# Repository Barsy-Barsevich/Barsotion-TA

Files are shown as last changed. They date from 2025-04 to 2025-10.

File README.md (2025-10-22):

# Barsotion-TA
Board computer for model rockets, the 11th board after Berkut

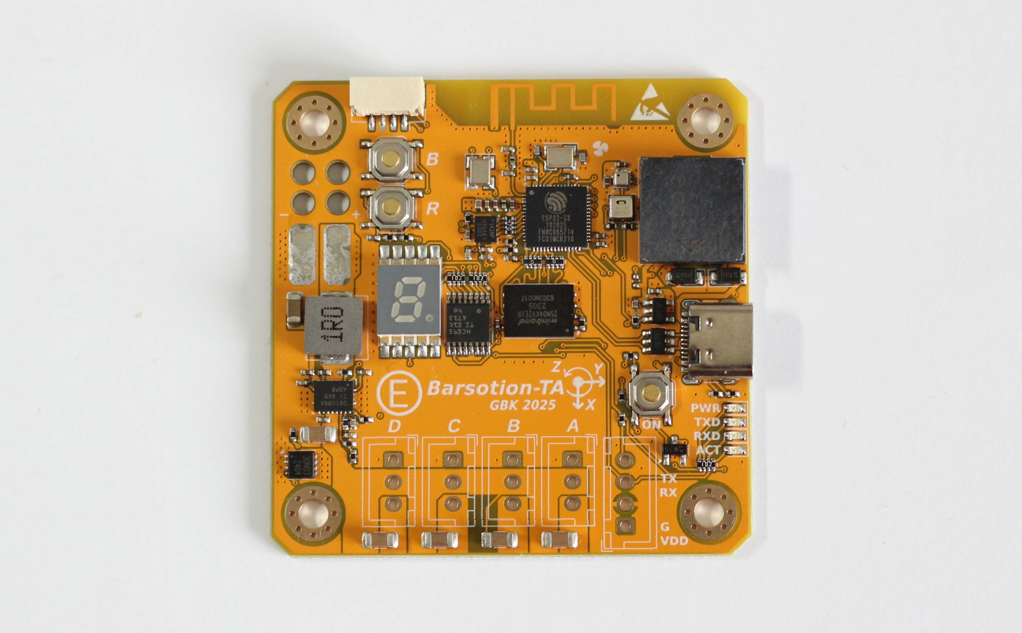
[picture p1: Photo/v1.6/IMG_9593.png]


## ⚡️Features
- Dual-core 240MHz Xtensa processor (in ESP32-S3)
- 512 MB log flash
- Up to 8kHz IMU cycle frequency
- Barometer, thermometer, hygrometer
- Onboard DC-DC pull-up converter for servos
- 2.4GHz Wi-Fi / Bluetooth / BLE antenna

## ⚡️Manual
- [EA&TA_user_manual_revD.pdf (newest revision)](./Manual/EA&TA_user_manual_revD.pdf)
- [EA&TA_user_manual_revC.pdf](./Manual/EA&TA_user_manual_revC.pdf)
- [EA&TA_user_manual_preliminary_edition_revB.pdf](./Manual/EA&TA_user_manual_preliminary_edition_revB.pdf)
- [EA&TA_user_manual_preliminary_edition_revA.pdf](./Manual/EA&TA_user_manual_preliminary_edition_revA.pdf)

## ⚡️Software
- [EA & TA software packet](https://github.com/Barsy-Barsevich/Barsotion-xA-software)

## ⚡️Continious progress
- [Previous board: Barsotion-EA](https://github.com/Barsy-Barsevich/Barsotion-EA)
- [Previous board: Barsotion-AH4](https://github.com/Barsy-Barsevich/Barsotion-AH4)

## ⚡️Schematic
[Full electrical schematic in .pdf](./Schematic/Barsotion-TA_Schematic_v1.6.pdf)
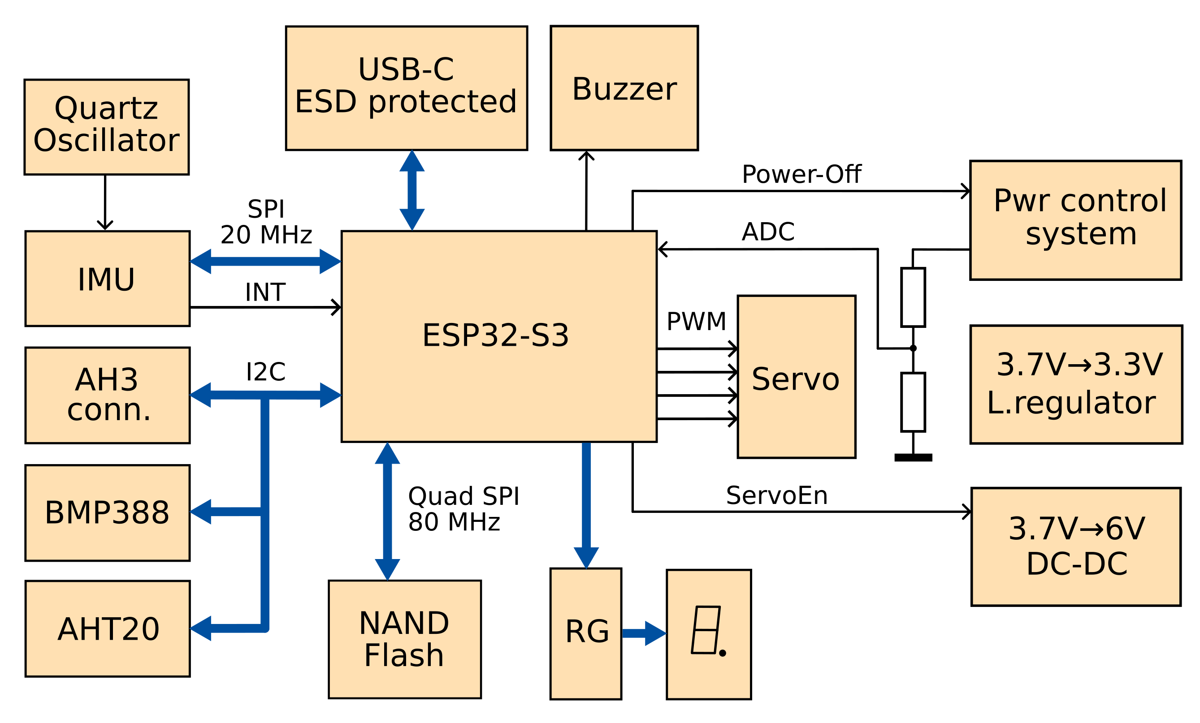
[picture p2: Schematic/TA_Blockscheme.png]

## ⚡️Parameters
- Microcontroller: ESP32-S3FN8 (2x Xtensa LX7 core)
- Clock frequency: 240MHz
- Gyroscope: on-board ICM-42688-P (SPI, interrupt channel)
- Barometer: on-board, BMP388 (I2C)
- Hygrometer: on-board, AHT20 (I2C)
- Memory: 4Gbit SPI NAND Flash W25N04KVZEIG (Quad SPI)
- Quartz Gyroscope's ODR frequency stabilization
- 2.4GHz Wi-Fi / Bluetooth / BLE antenna

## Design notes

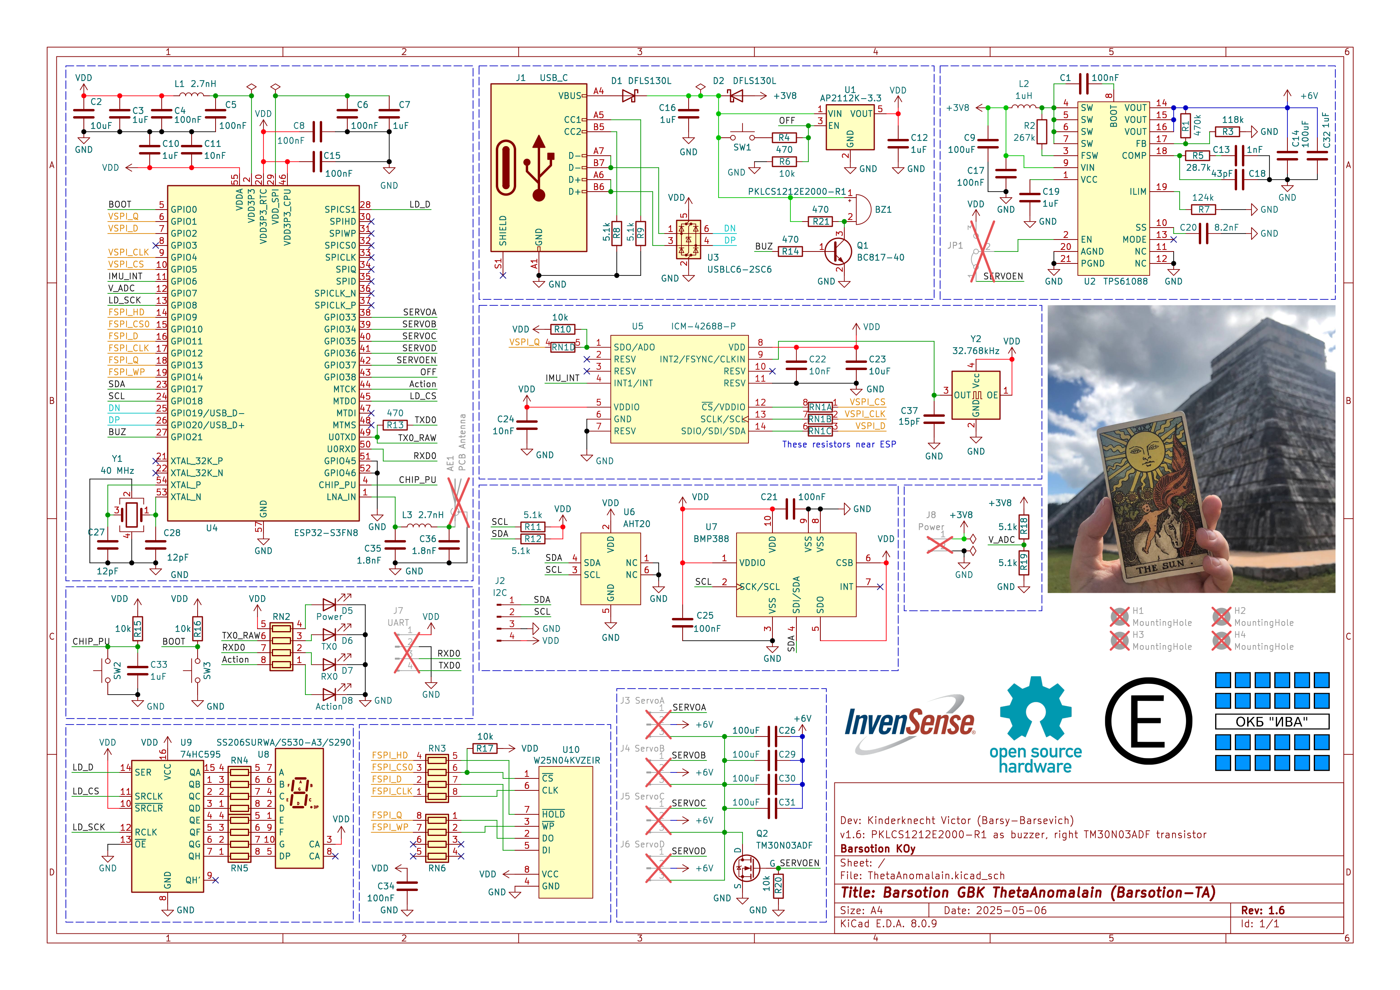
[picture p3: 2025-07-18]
Schematic/Barsotion-TA_Schematic_v1.6.png

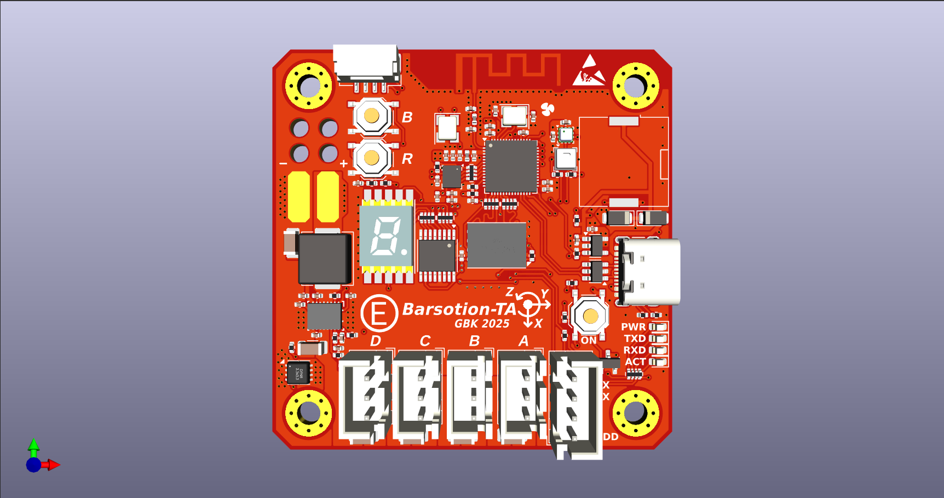
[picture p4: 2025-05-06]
Photo/v1.6/Screenshot at 2025-05-06 14-15-10.png

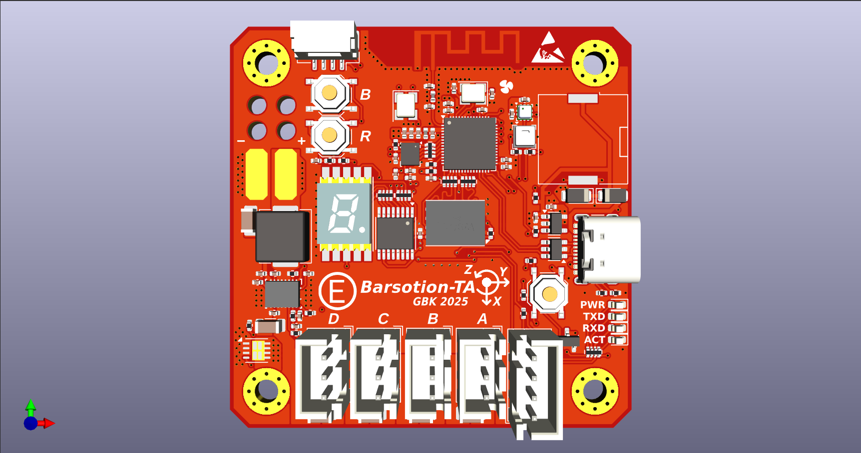
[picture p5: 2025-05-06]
Photo/v1.6/Screenshot at 2025-05-06 03-56-42.png

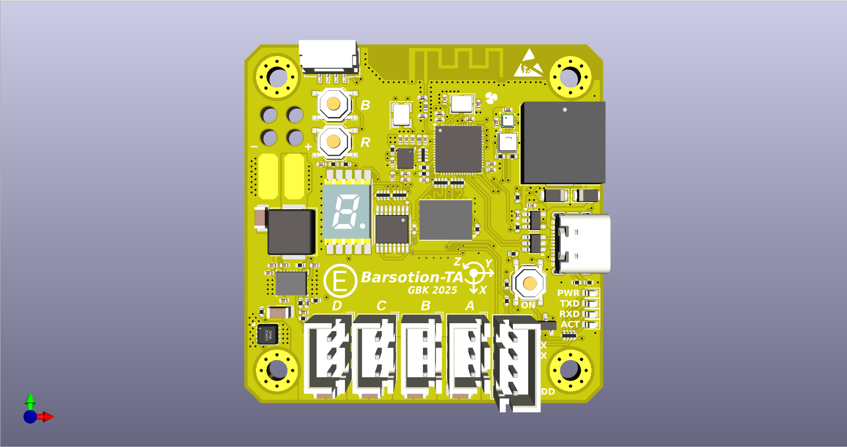
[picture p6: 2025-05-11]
Photo/v1.6/Screenshot at 2025-05-09 21-59-08.png

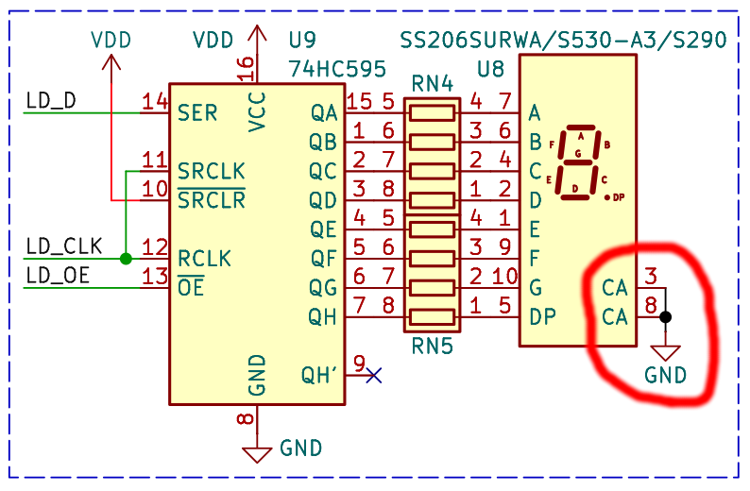
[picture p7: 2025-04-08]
Errors_EA/Screenshot at 2025-04-03 12-46-04.png

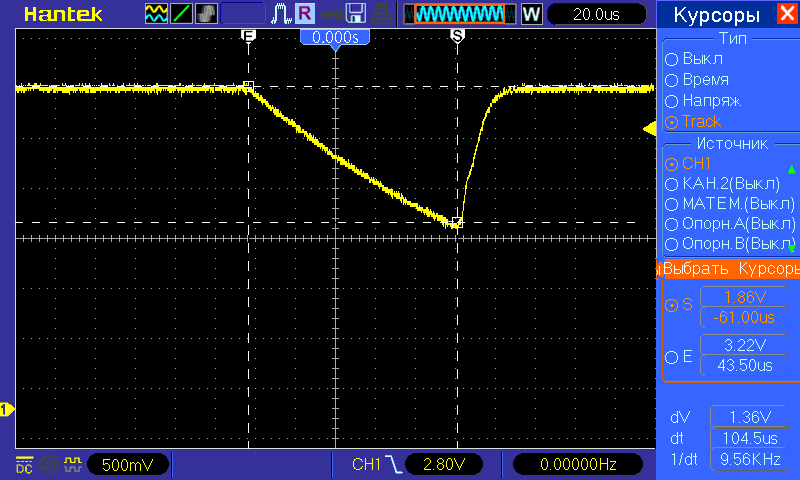
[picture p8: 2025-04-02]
Errors_EA/EA_Err1_Poweroff/VDD_line_when_POWER-OFF_command.bmp

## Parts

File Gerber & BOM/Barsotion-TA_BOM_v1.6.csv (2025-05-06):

Reference | Value | Datasheet | Footprint | Qty | Описание | Mfr.Part
BZ1 | PKLCS1212E2000-R1 | https://www.lcsc.com/datasheet/lcsc_datasheet_2410010302_Murata-Electronics-PKLCS1212E2000-R1_C184513.pdf | Buzzer_Beeper:Buzzer_Murata_PKLCS1212E | 1 | Buzzer | PKLCS1212E2000-R1
C1,C4,C5,C6,C8,C15,C17,C21,C25,C34 | 100nF | ~ | Capacitor_SMD:C_0402_1005Metric | 10 | Unpolarized capacitor
C2,C23 | 10uF | ~ | Capacitor_SMD:C_0402_1005Metric | 2 | Unpolarized capacitor
C3,C7,C10,C12,C16,C19,C32,C33 | 1uF | ~ | Capacitor_SMD:C_0402_1005Metric | 8 | Unpolarized capacitor
C9,C14,C26,C29,C30,C31 | 100uF | ~ | Capacitor_SMD:C_1206_3216Metric | 6 | Unpolarized capacitor
C11,C22,C24 | 10nF | ~ | Capacitor_SMD:C_0402_1005Metric | 3 | Unpolarized capacitor
C13 | 1nF | ~ | Capacitor_SMD:C_0402_1005Metric | 1 | Unpolarized capacitor
C18 | 43pF | ~ | Capacitor_SMD:C_0402_1005Metric | 1 | Unpolarized capacitor
C20 | 8.2nF | ~ | Capacitor_SMD:C_0402_1005Metric | 1 | Unpolarized capacitor
C27,C28 | 12pF | ~ | Capacitor_SMD:C_0402_1005Metric | 2 | Unpolarized capacitor
C35,C36 | 1.8nF | ~ | Capacitor_SMD:C_0402_1005Metric | 2 | Unpolarized capacitor
C37 | 15pF | ~ | Capacitor_SMD:C_0402_1005Metric | 1 | Unpolarized capacitor
D1,D2 | DFLS130L | ~ | Diode_SMD:D_PowerDI-123 | 2 | Schottky diode
D5 | Power | ~ | LED_SMD:LED_0603_1608Metric | 1 | Yellow Light emitting diode | TJ-S1608CY6T5ALC9Y-A5
D6 | TX0 | ~ | LED_SMD:LED_0603_1608Metric | 1 | Yellow Light emitting diode | TJ-S1608CY6T5ALC9Y-A5
D7 | RX0 | ~ | LED_SMD:LED_0603_1608Metric | 1 | Yellow Light emitting diode | TJ-S1608CY6T5ALC9Y-A5
D8 | Action | ~ | LED_SMD:LED_0603_1608Metric | 1 | Yellow Light emitting diode | TJ-S1608CY6T5ALC9Y-A5
J1 | USB_C | https://www.usb.org/sites/default/files/documents/usb_type-c.zip | Connector_USB:USB_C_Receptacle_GCT_USB4105-xx-A_16P_TopMnt_Horizontal | 1 | USB 2.0-only 16P Type-C Receptacle connector, mfr part TYPE C-DB-116PWB | TYPE C-DB-116PWB
J2 | I2C | ~ | Connector_JST:JST_GH_SM04B-GHS-TB_1x04-1MP_P1.25mm_Horizontal | 1 | Generic connector, single row, 01x04, script generated | A1257WR-S-4P
L1,L3 | 2.7nH | https://www.lcsc.com/datasheet/lcsc_datasheet_2409302232_APV-APH0630T1R0M_C5349700.pdf | Inductor_SMD:L_0402_1005Metric | 2 | Inductor
L2 | 1uH | https://www.lcsc.com/datasheet/lcsc_datasheet_2409302232_APV-APH0630T1R0M_C5349700.pdf | Inductor_SMD:L_APV_APH0630 | 1 | Power inductor | APH0630T1R0M
Q1 | BC817-40 | https://www.onsemi.com/pub/Collateral/BC818-D.pdf | Package_TO_SOT_SMD:SOT-23 | 1 | 0.8A Ic, 45V Vce, NPN Transistor, SOT-23
Q2 | TM30N03ADF | https://www.lcsc.com/datasheet/lcsc_datasheet_2411121142_Tritech-MOS-TM30N03ADF_C7422839.pdf | CustomPackage:PDFN3x3-8L | 1 | N-MOSFET transistor, TM30N03ADF | TM30N03ADF
R1 | 470k | ~ | Resistor_SMD:R_0402_1005Metric | 1 | Resistor
R2 | 267k | ~ | Resistor_SMD:R_0402_1005Metric | 1 | Resistor
R3 | 118k | ~ | Resistor_SMD:R_0402_1005Metric | 1 | Resistor
R4,R13,R14,R21 | 470 | ~ | Resistor_SMD:R_0402_1005Metric | 4 | Resistor
R5 | 28.7k | ~ | Resistor_SMD:R_0402_1005Metric | 1 | Resistor
R6,R10,R15,R16,R17,R20 | 10k | ~ | Resistor_SMD:R_0402_1005Metric | 6 | Resistor
R7 | 124k | ~ | Resistor_SMD:R_0402_1005Metric | 1 | Resistor
R8,R9,R11,R12,R18,R19 | 5.1k | ~ | Resistor_SMD:R_0402_1005Metric | 6 | Resistor
RN1 | 47 | ~ | Resistor_SMD:R_Array_Convex_4x0402 | 1 | 4 resistor network, parallel topology, split
RN2,RN4,RN5 | 1k | ~ | Resistor_SMD:R_Array_Convex_4x0402 | 3 | 4 resistor network, parallel topology
RN3,RN6 | 0 | ~ | Resistor_SMD:R_Array_Convex_4x0402 | 2 | 4 resistor network, parallel topology
SW1,SW2,SW3 | TS-1187A-B-A-B | ~ | Button_Switch_SMD:SW_Push_1P1T_XKB_TS-1187A | 3 | TS-1187A-B-A-B | TS-1187A-B-A-B
U1 | AP2112K-3.3 | https://www.diodes.com/assets/Datasheets/AP2112.pdf | Package_TO_SOT_SMD:SOT-23-5 | 1 | 600mA low dropout linear regulator, with enable pin, 3.8V-6V input voltage range, 3.3V fixed positive output, SOT-23-5 | AP2112K-3.3TRG1
U2 | TPS61088 |  | UltraLibrarian:RHL0020A | 1 | Texas Instruments DC-DC Pullup converter | TPS61088RHLR
U3 | USBLC6-2SC6 | https://www.st.com/resource/en/datasheet/usblc6-2.pdf | Package_TO_SOT_SMD:SOT-23-6 | 1 | Very low capacitance ESD protection diode, 2 data-line, SOT-23-6 | USBLC6-2SC6
U4 | ESP32-S3FN8 | https://www.espressif.com/sites/default/files/documentation/esp32-s3_datasheet_en.pdf | Package_DFN_QFN:QFN-56-1EP_7x7mm_P0.4mm_EP4x4mm | 1 | Microcontroller, Wi-Fi 802.11b/g/n, Bluetooth, 32bit | ESP32-S3FN8
U5 | ICM-42688-P | https://invensense.tdk.com/wp-content/uploads/2020/04/ds-000347_icm-42688-p-datasheet.pdf | Package_LGA:LGA-14_3x2.5mm_P0.5mm_LayoutBorder3x4y | 1 | InvenSense High-precision 6-axes gyroscope accelerometer | ICM-42688-P
U6 | AHT20 | https://files.seeedstudio.com/wiki/Grove-AHT20_I2C_Industrial_Grade_Temperature_and_Humidity_Sensor/AHT20-datasheet-2020-4-16.pdf | CustomPackage:AHT20 | 1 | Digital hygrometer | AHT20
U7 | BMP388 | https://pdf1.alldatasheet.com/datasheet-pdf/download/1132070/BOSCH/BMP388.html | CustomPackage:BMP388_v2 | 1 | Bosch barometer thermometer | BMP388
U8 | SS206SURWA/S530-A3/S290 | https://www.lcsc.com/datasheet/lcsc_datasheet_2409302134_Everlight-Elec-SS206SURWA-S530-A3-S290_C19188062.pdf | CustomPackage:SS206SURWA | 1 | One digit 7 segment hyper red LED, common anode | SS206SURWA/S530-A3/S290
U9 | 74HC595 | http://www.ti.com/lit/ds/symlink/sn74hc595.pdf | Package_SO:TSSOP-16_4.4x5mm_P0.65mm | 1 | 8-bit serial in/out Shift Register 3-State Outputs | SN74HC595PWR
U10 | W25N04KVZEIR | https://www.lcsc.com/datasheet/lcsc_datasheet_2411121118_Winbond-Elec-W25N04KVZEIR_C5342170.pdf | Package_SON:WSON-8-1EP_8x6mm_P1.27mm_EP3.4x4.3mm | 1 | SPI NAND Flash 4Gbit chip | W25N04KVZEIR
Y1 | 40 MHz | ~ | Crystal:Crystal_SMD_3225-4Pin_3.2x2.5mm | 1 | Four pin crystal, GND on pins 2 and 4 | X322540MPB4SI
Y2 | 32.768kHz | https://www.lcsc.com/datasheet/lcsc_datasheet_2407310922_YXC-Crystal-Oscillators-OK2EL89CJI-111YLC-32-768K_C5280579.pdf | Oscillator:Oscillator_SMD_SeikoEpson_SG8002CE-4Pin_3.2x2.5mm | 1 | CMOS Clock Oscillator | OK2EL89CJI-111YLC-32.768K

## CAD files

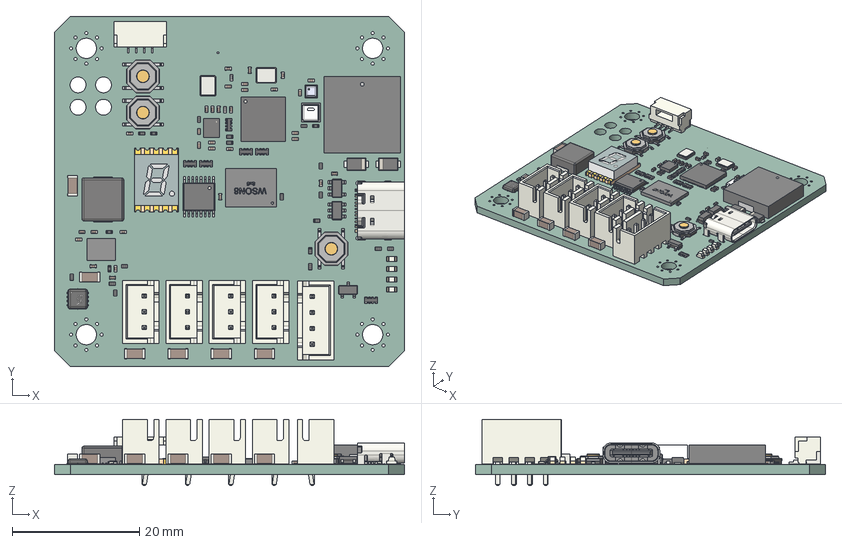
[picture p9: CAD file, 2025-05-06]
Step/Barsotion-TA_STEP_v1.6.step
55.0 x 55.0 x 10.4 mm
LED_0603_1608Metric x 4
R_0402_1005Metric x 21
RHL0020A_ASM
JST_B3B_XH_A x 4
C_1206_3216Metric x 6
SW_SPST_TL3342 x 3
TSSOP_16_44x5mm_P065mm
SOT_23
C_0402_1005Metric x 31
L_APV_APH0630
L_0402_1005Metric x 2
JST_B4B_XH_A
Crystal_SMD_3225-4Pin_3.2x2.5mm x 2
ACSC02-41SURKWA-F01
R_Array_Convex_4x0402 x 6
AHT20 Sensor v0
LGA_14_3x25mm_P05mm_LayoutBorder3x4y
JST_SM04B_GHS_TB
SOT_23_5
PDFN3333 (DFN8 3.3x3.3)
SOT_23_6
CQ assembly
WSON8-8x6
D_PowerDI_123 x 2
BMP388
USB_C_Receptacle_16P_TopMnt_Horizontal_GCT_USB4105-xx-A
ThetaAnomalain_PCB

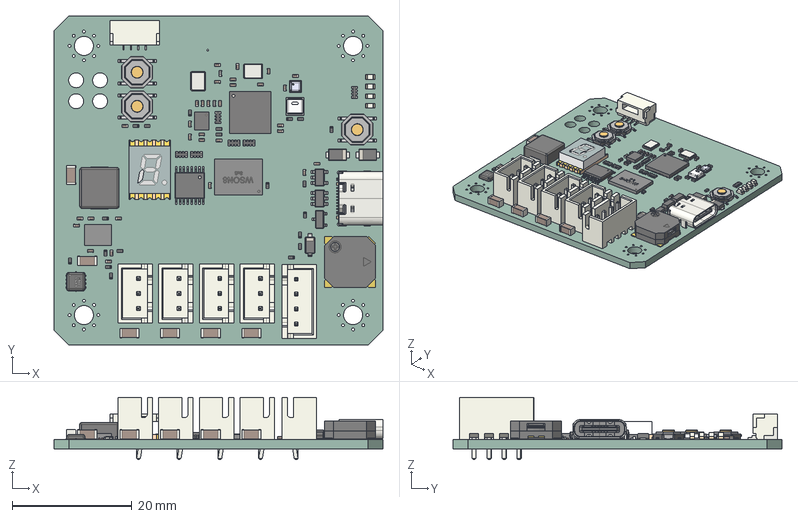
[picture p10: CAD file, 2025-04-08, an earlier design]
Step/Barsotion-TA_STEP_v1.3.step
55.0 x 55.0 x 10.4 mm
LED_0603_1608Metric x 4
R_0402_1005Metric x 20
RHL0020A_ASM
JST_B3B_XH_A x 4
C_1206_3216Metric x 6
SW_SPST_TL3342 x 3
D_SOD_123
TSSOP_16_44x5mm_P065mm
SOT_23
C_0402_1005Metric x 31
L_APV_APH0630
L_0402_1005Metric x 2
JST_B4B_XH_A
Crystal_SMD_3225-4Pin_3.2x2.5mm x 2
ACSC02-41SURKWA-F01
R_Array_Convex_4x0402 x 6
AHT20 Sensor v0
CMT-8503-87_90
LGA_14_3x25mm_P05mm_LayoutBorder3x4y
JST_SM04B_GHS_TB
SOT_23_5
PDFN3333 (DFN8 3.3x3.3)
SOT_23_6
CQ assembly
WSON8-8x6
D_PowerDI_123 x 2
BMP388
USB_C_Receptacle_16P_TopMnt_Horizontal_GCT_USB4105-xx-A
ThetaAnomalain_PCB

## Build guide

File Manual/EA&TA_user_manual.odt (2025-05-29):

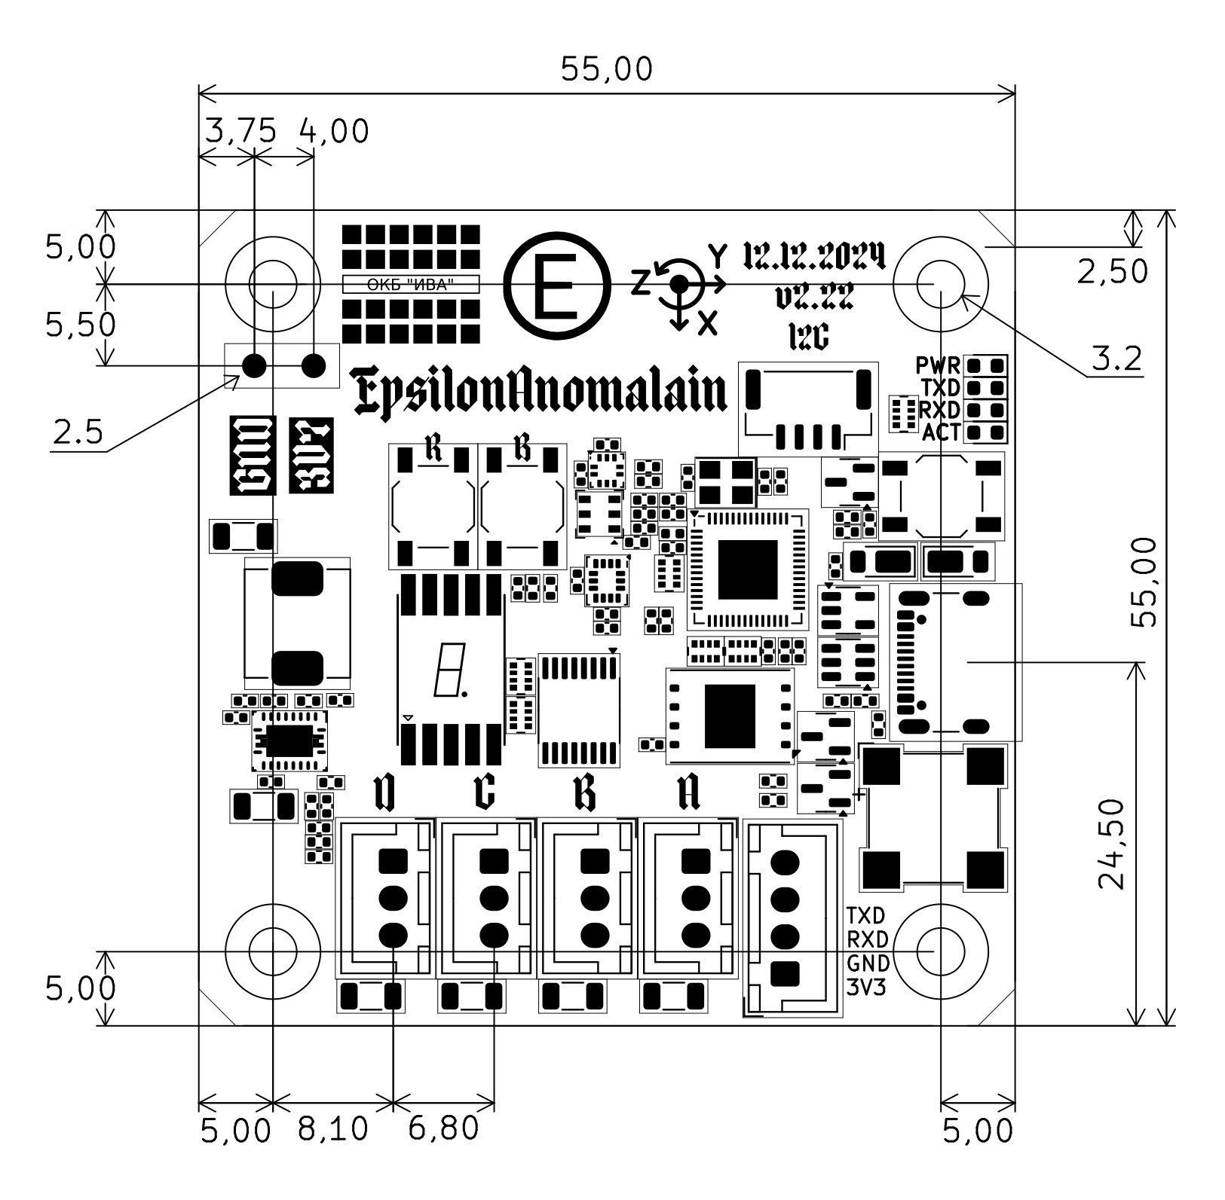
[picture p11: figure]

Figure 4: EA dimentions

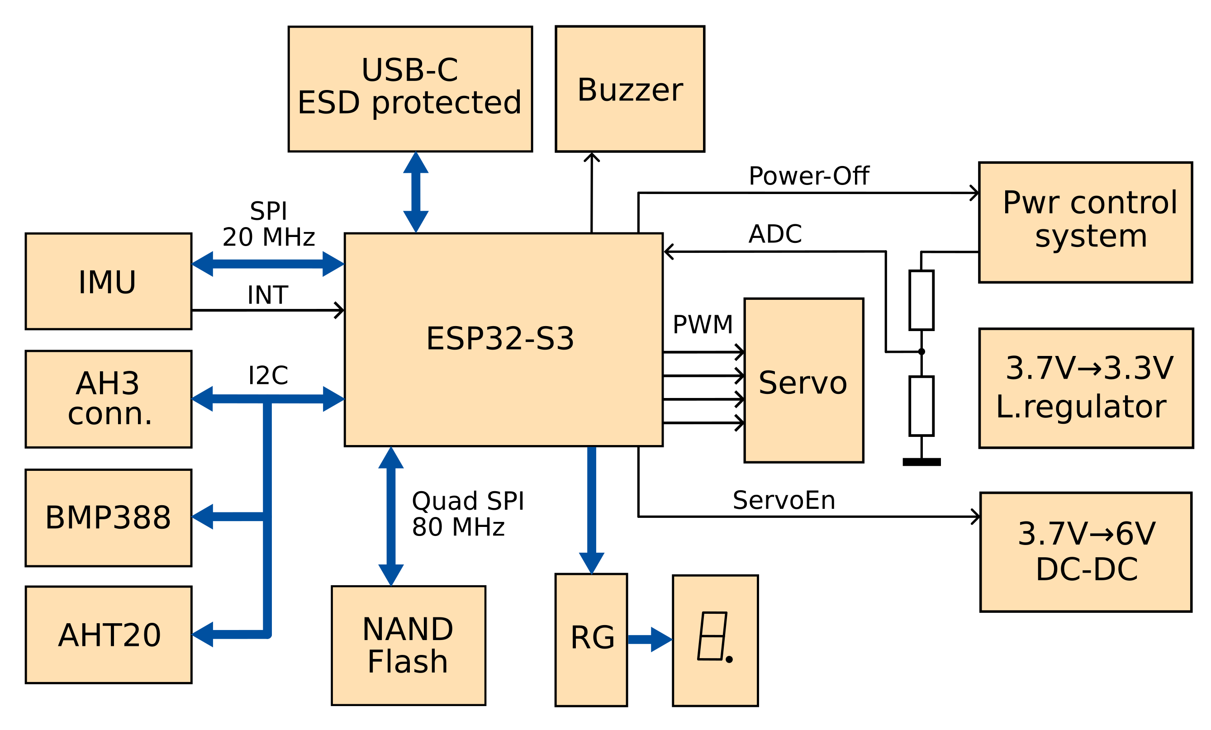
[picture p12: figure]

Figure 5: EA structural schematic

Barsotion EA & TA:

User manual

## Overview

The EA & TA board computers as a part of Barsotion xAnomalain series are the devices created to control small model rockets flight and write down flight parameters. It was developed for the OKB “Iva” Pike rocket project.

These computers are the logical continuation of Barsotion GBK DeltaAnomalain board computer, used in OKB “Iva” Kilka project.

For the EA & TA developing, some radical principles were adopted:

- As possible new components.
- Manufacturability and simply usage.
- Aesthetics and sophistication.

“By the Will of God and according to the plan”

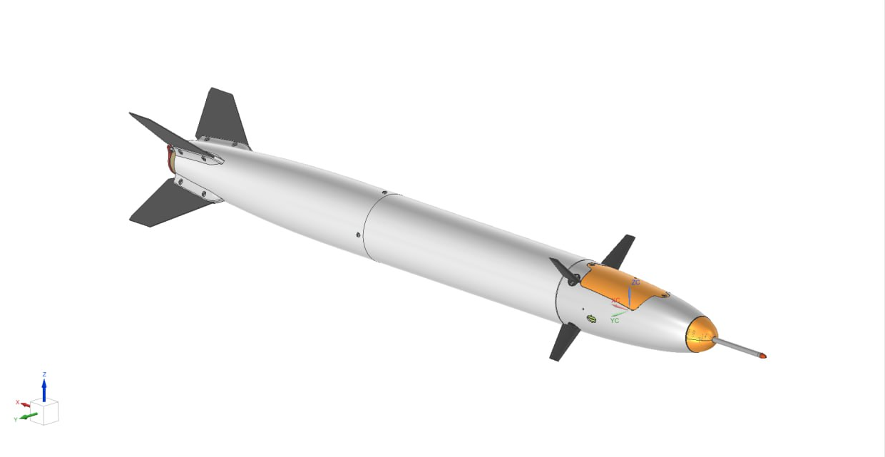
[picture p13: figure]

Figure 1: Pike rocket explained view

## EA hardware description

The Barsotion GBK EpsilonAnomalain boards (Barsotion-EA) was created as a part of model rocket project Pike.

### EA Concepts

The Pike rocket has the following view:

The EA board computer (GBK) should be located at the nose of rocket, consist of one board and placed longitudinally. The power source is the 3.7 V 18650 battery with typical capacity around 3000 mA*h. The board computer should contain following sensors:

Figure 2: Pike rocket view

- Gyroscope & accelerometer (ICM-42688-P was chosen), connected via SPI, that is important because of necessity of ensuring high data read speed;
- Barometer (BMP388 was chosen);
- AH3 air speed sensor connector (4-pin, 3,3V, GND, SDA, SCL);
- Hygrometer (AHT20 was chosen).

The microcontroller should be enough rapid for processing gyroscope’s data a few thousand times per second. Reading data from the gyroscope should be synchronized with gyroscope’s interrupt channel.

Barometer and hygrometer data reading interrupt synchronization is not needed.

The board computer should contain a flash memory chip, the capacity should not be less than 1 Gbit.

The board computer should have connectors for four MG90S servos. Also it should have a DC-DC boost voltage converter to provide servo feeding. The board computer should can power down servos if they are not used, because servos have a significant static power consumption.

The board computer should can measure battery voltage and have a power-off option, that allows to power down system by the microcontroller command.

The board computer should switch on by special button pressing. It is supposed that the computer will be connected to the battery a long time before the start so that long working not wanted. The computer should be switched on shortly before the start for saving the battery charge.

The computer should have a small seven-segment led indicator on the board for system status indication and also 4 LEDs:

- Power 3.3 V indication LED;
- TXD0 LED;
- RXD0 LED;
- User-driven LED.

The power indication helps to control the computer is working or not, TXD and RXD indication helps to control the data transmission progress. User-driven LED is needed for simplifying the debug process and improving the computer using user’s experience.

Also the board computer should have a buzzer that needed to signal when the rocked landed and waits to be found.

### EA Realization

The Barsotion-EA has following characteristics:

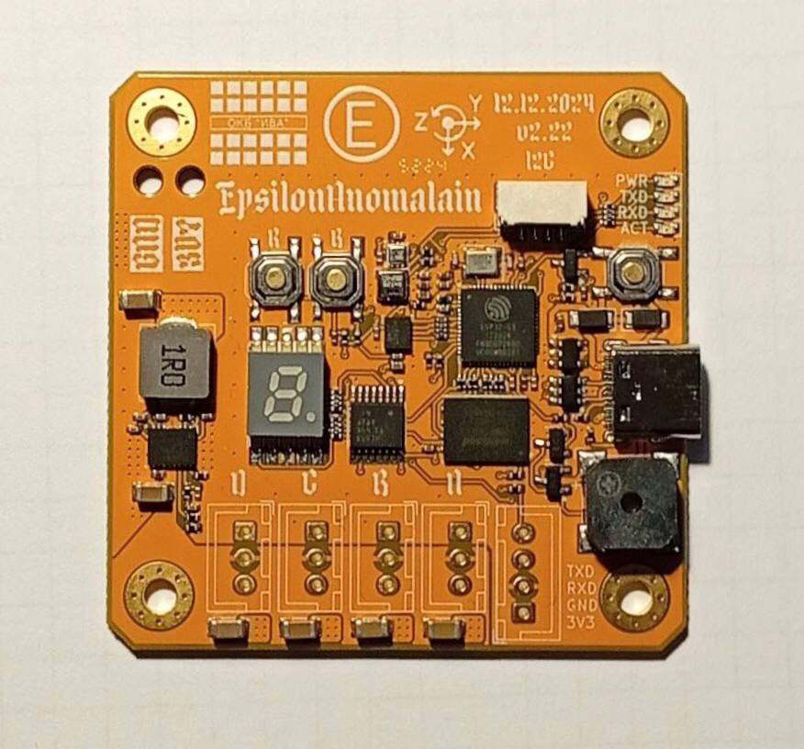
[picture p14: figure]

Figure 3: EA explained view

- Microcontroller: ESP32-S3FN8;
- Gyroscope & accelerometer: ICM-42688-P;
- Barometer: BMP388;
- Hygrometer: AHT20;
- AH3 board I2C connector;
- Buzzer for sound indication;
- Seven-segment LED indicator driven by 74HC595 shift register;
- USB-C for flashing & debug;
- SPI NAND Flash memory chip W25N01GVZEIG, the capacity is 1 Gbit;
- DC-DC boost voltage converter based on TPS61088 for servo feeding, the schematic is calculated and topology drawn for continious 3 A current;
- Four servo connectors.

### EA Dimentions

### EA Structural schematic

### EA Topology

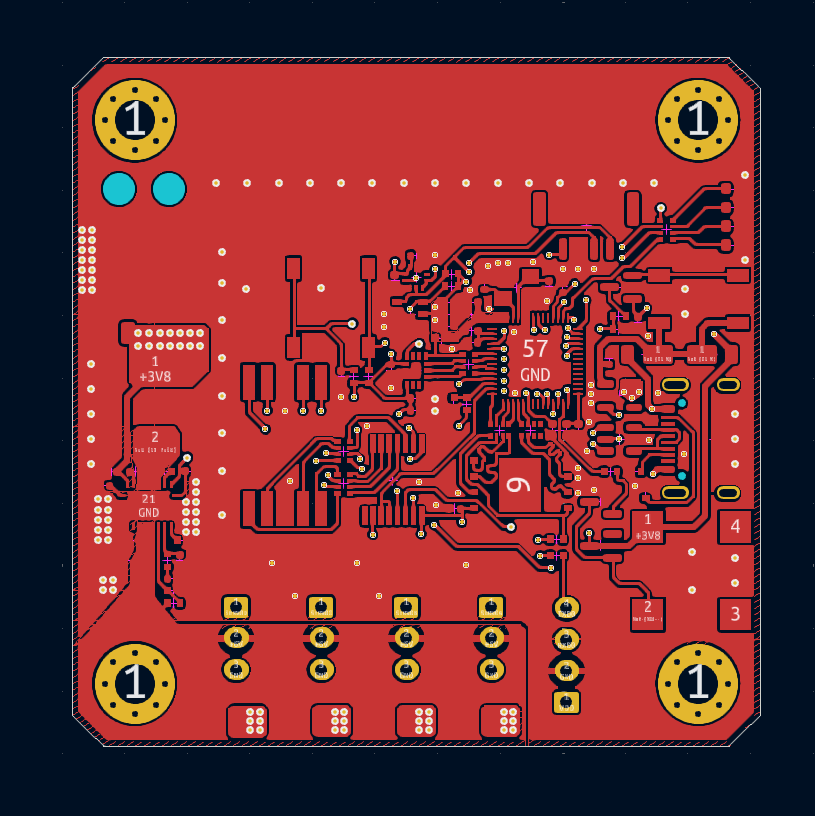
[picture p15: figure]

Figure 6: EA Layer 1 - Top signal

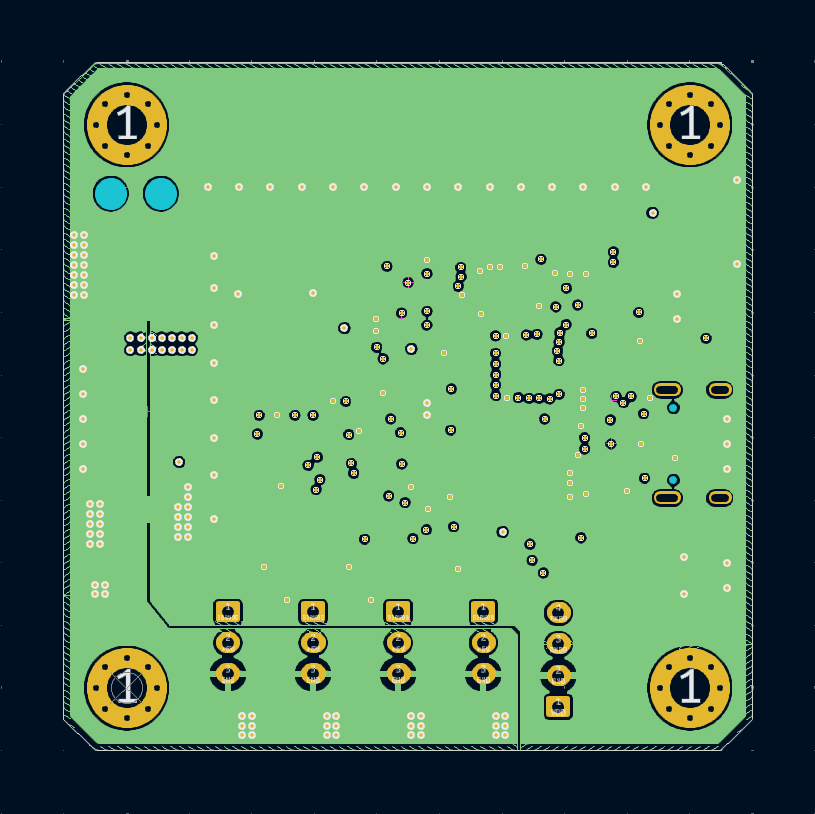
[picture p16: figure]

Figure 7: EA Layer 2 - GND

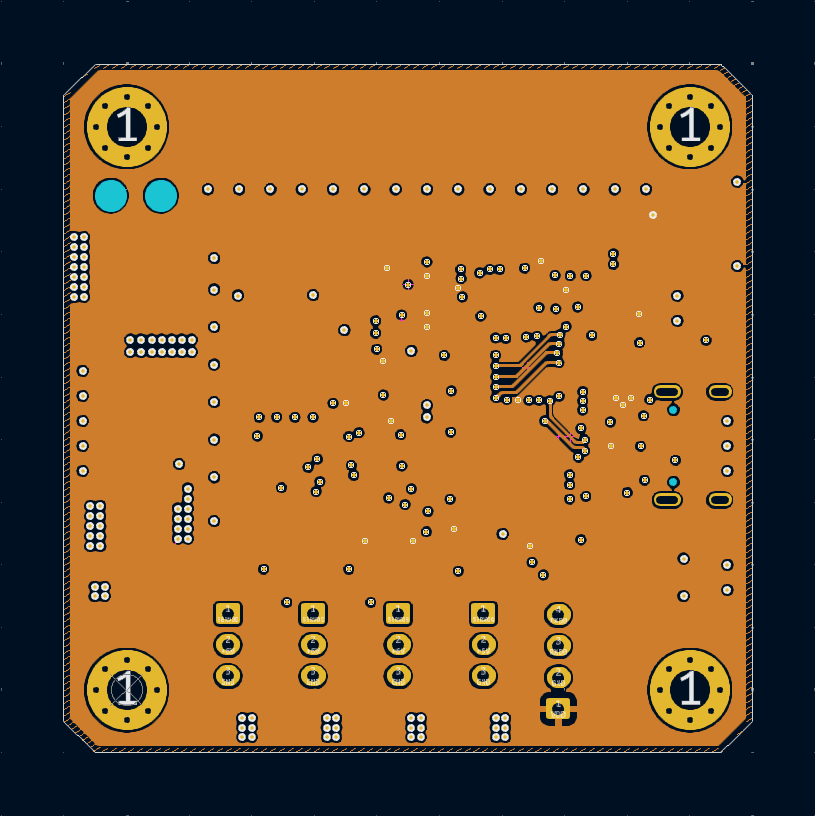
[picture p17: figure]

Figure 8: EA Layer 3 - Power

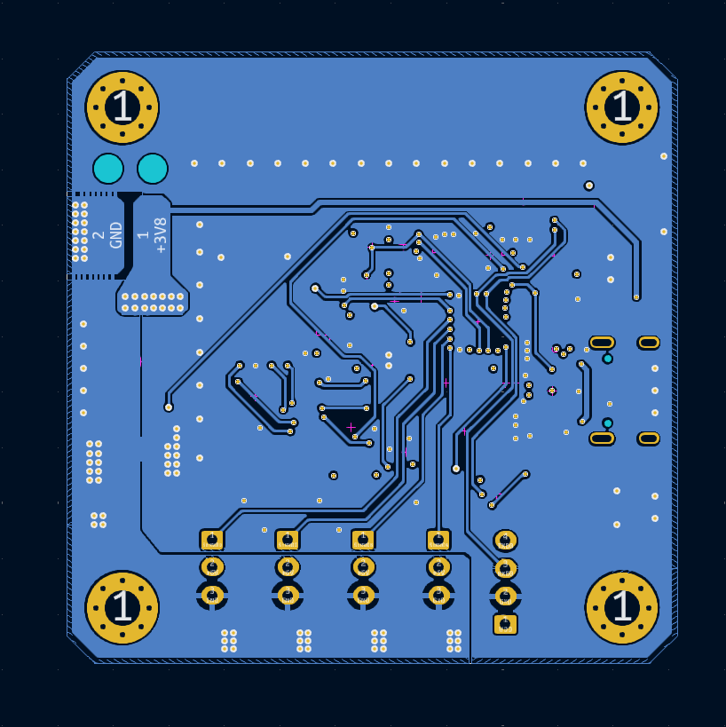
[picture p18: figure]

Figure 9: EA Layer 4 - Bottom signal

### EA Errata

While the EA tests some errors was finded.

#### EA_ERR1_Anode

The LED module’s common anodes should be routed to +3.3 V power supply, however they are wired to the ground. That is a reason why the led indicator on the EA does not work.


Figure 10: EA_ERR1_Anode

#### EA_ERR2_Poweroff

The EA boards have a hardware ability to power-off themselves by microcontroller command. It is useful if the battery voltage is low.

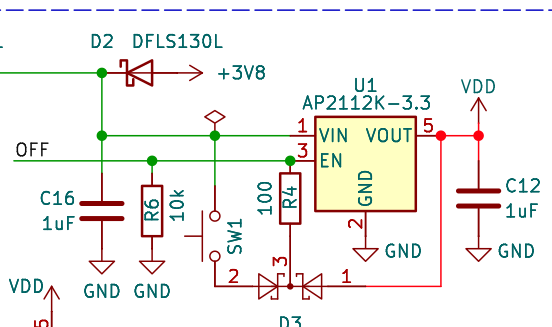
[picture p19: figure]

Figure 11: EA_ERR2_Poweroff

The power-off function does not work properly. When the OFF pin (GPIO38) is initialized as output and the logic 0 routed to this pin, the voltage on the VDD line decrease down to 1.8-1.9 V level, after that the GPIO block in the microcontroller stops the working, the OFF pin goes to tri-state condition, VDD capacitors’ residual charge provides a high level on the regulator’s EN pin and the device restarts.

#### EA_ERR3_Servo_supply

Figure 13: VDD line after POWER-OFF command receiving

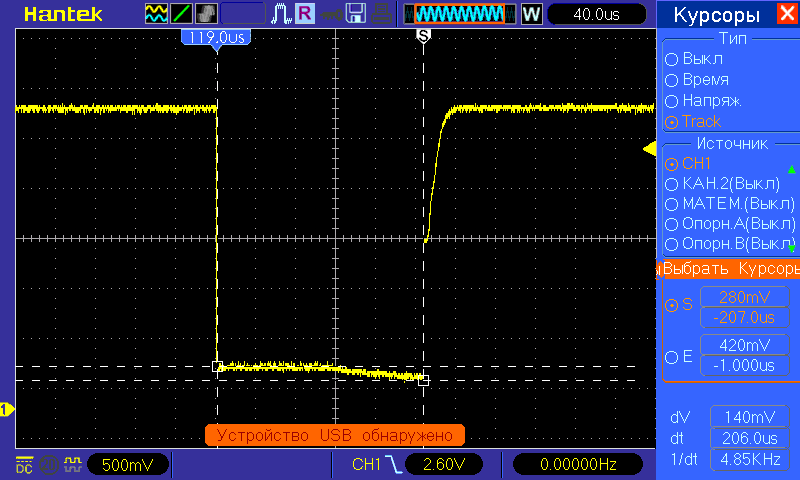
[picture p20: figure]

Figure 12: OFF line after POWER-OFF command receiving

This error caused from mistake of understanding the TPS61088 EN (Enable) pin function.

The SERVOEN line is wired directly from microcontroller to TPS61088’s EN pin. While the EA developing it means that if the EN pin is not active, there is no voltage on the 6 V output servo feeding line. However the EN pin only enables voltage conversion, not current passing by the converter IC.

EN pin enables driving the switch. If it is not active, switch is always unlocked, so the converter does not work. However the voltage still can pass through the inductor and diode to the servos. The solving of the problem is to add the transistor to the servo feeding circuit that can break the circuit if it is needed.

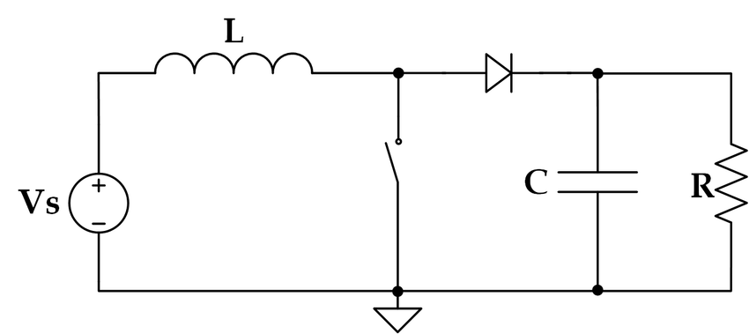
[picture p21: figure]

Figure 14: Simplified boost converter circuit

### EA GitHub repository

Barsotion-EA’s KiCad sources, full schematic, pindefs-file are located at a project GitHub repository (https://github.com/Barsy-Barsevich/Barsotion-EA).

## TA hardware description

### TA Concepts

The main goal of the TA creation is to fix the EA schematic error and problems. The most of device requirements are the same as for EA. However some extra features was wanted:

- Add the ICM-42688-P ODR frequency quartz stabilization
- Add 2.4 GHz WiFi / Bluetooth / BLE antenna
- Use 4 Gbit Flash chip instead of 1 Gbit
- Change the buzzer connection for allowing the buzzer to work when the board connected to the computer via USB (on the EA board the buzzer can make sound only if the battery connected)

According the EA&TA software architecture, the core 1’s cycle time depends on the ICM-42688-P INT1 pin period that is the same as the maximum of accelerometer & gyroscope’s ODRs. By default, the ODR frequency is generated from internal RC-source with 1% accuracy. Usual way to get the cycle time is considered in subtraction previous system timer’s value from actual. The ESP32-S3’s system timer has 1-microsecond accuracy, that does not allows to use ODR 16 kHz or 32 kHz because their periods have non-integer values in microseconds (62.5 & 31.25 microseconds), that causes bigger integral errors while integrating (the tests show that 8 kHz ODR gives smaller integral errors than 16 kHz, which contradicts the theory of numerical methods). The solving of the problem can be in ODR frequency quartz stabilization. If it is used, the ODR frequency has 10 ppm accuracy, so allows to use a constant as the cycle time value.

The 2.4 GHz antenna addition is not needed for rocket project tasks, however this requirement was added for getting more experience in high-frequency circuits topology design.

After the EA tests a curious fact was found: there are W25N01 memory chip pin-to-pin compatible chips with more capacity, for example W25N04. So using memory with more capacity is wanted.

### TA Realization

Thus, the Barsotion-EA has following characteristics:

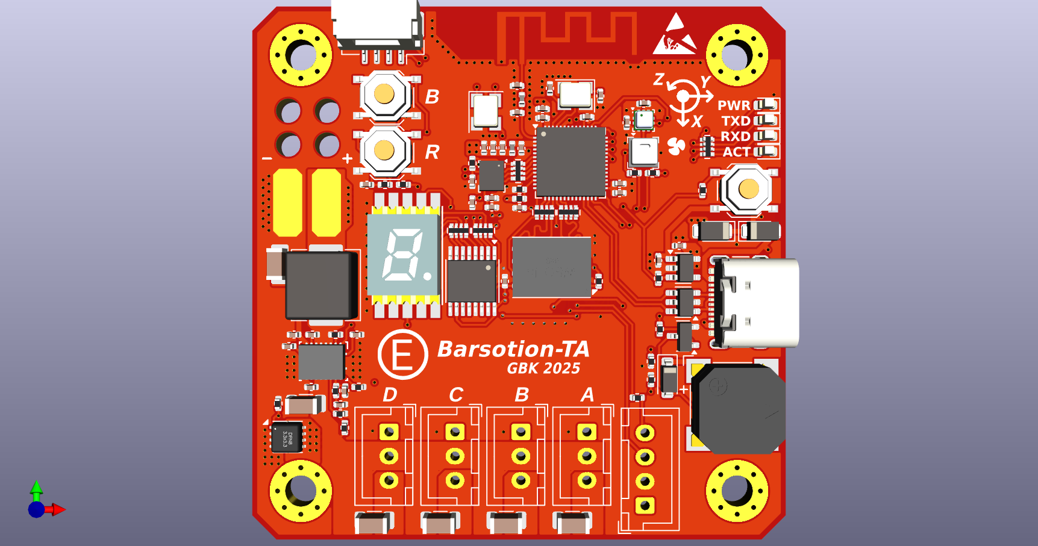
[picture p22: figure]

Figure 15: TA explained view

- Microcontroller: ESP32-S3FN8;
- 2.4 GHz Wi-Fi / Bluetooth / BLE antenna driven by ESP chip;
- Gyroscope & accelerometer: ICM-42688-P (quartz-stabilized ODR frequency);
- Barometer: BMP388;
- Hygrometer: AHT20;
- AH3 board I2C connector;
- Buzzer for sound indication;
- Seven-segment LED indicator driven by 74HC595 shift register;
- USB-C for flashing & debug;
- SPI NAND Flash memory chip W25N04KVZEIG, the capacity is 4 Gbit
- DC-DC boost voltage converter based on TPS61088 for servo feeding, the schematic is calculated and topology drawn for continious 3 A current;
- Servo powerdown ability thanks to transistor breaking the feeding line;
- Four servo connectors.

### TAv1.6

Because of BOM ambiguous interpretation a wrong buzzer was ordered, PKLCS1212E2000-R1 instead of CMT-8504-100-SMT-TR. The producing company agent told that they can deliver right buzzer, however CMT-8504-100-SMT-TR delivering takes two weeks that is much. Also, a schematic error was found in TA boards: wrong transistor Q2 connection caused by incorrect package pinout.

It was decided to re-release the TA boards. A schematic, topology, Gerber, BOM, PNP was fixed and adopted for PKLCS1212E2000-R1 usage. New TA version was indexed as “TA v1.6” or “TAv1.6”.

Figure 16: TAv1.6 explained view

### TA Dimentions

Dimentions are common for TA & TAv1.6.

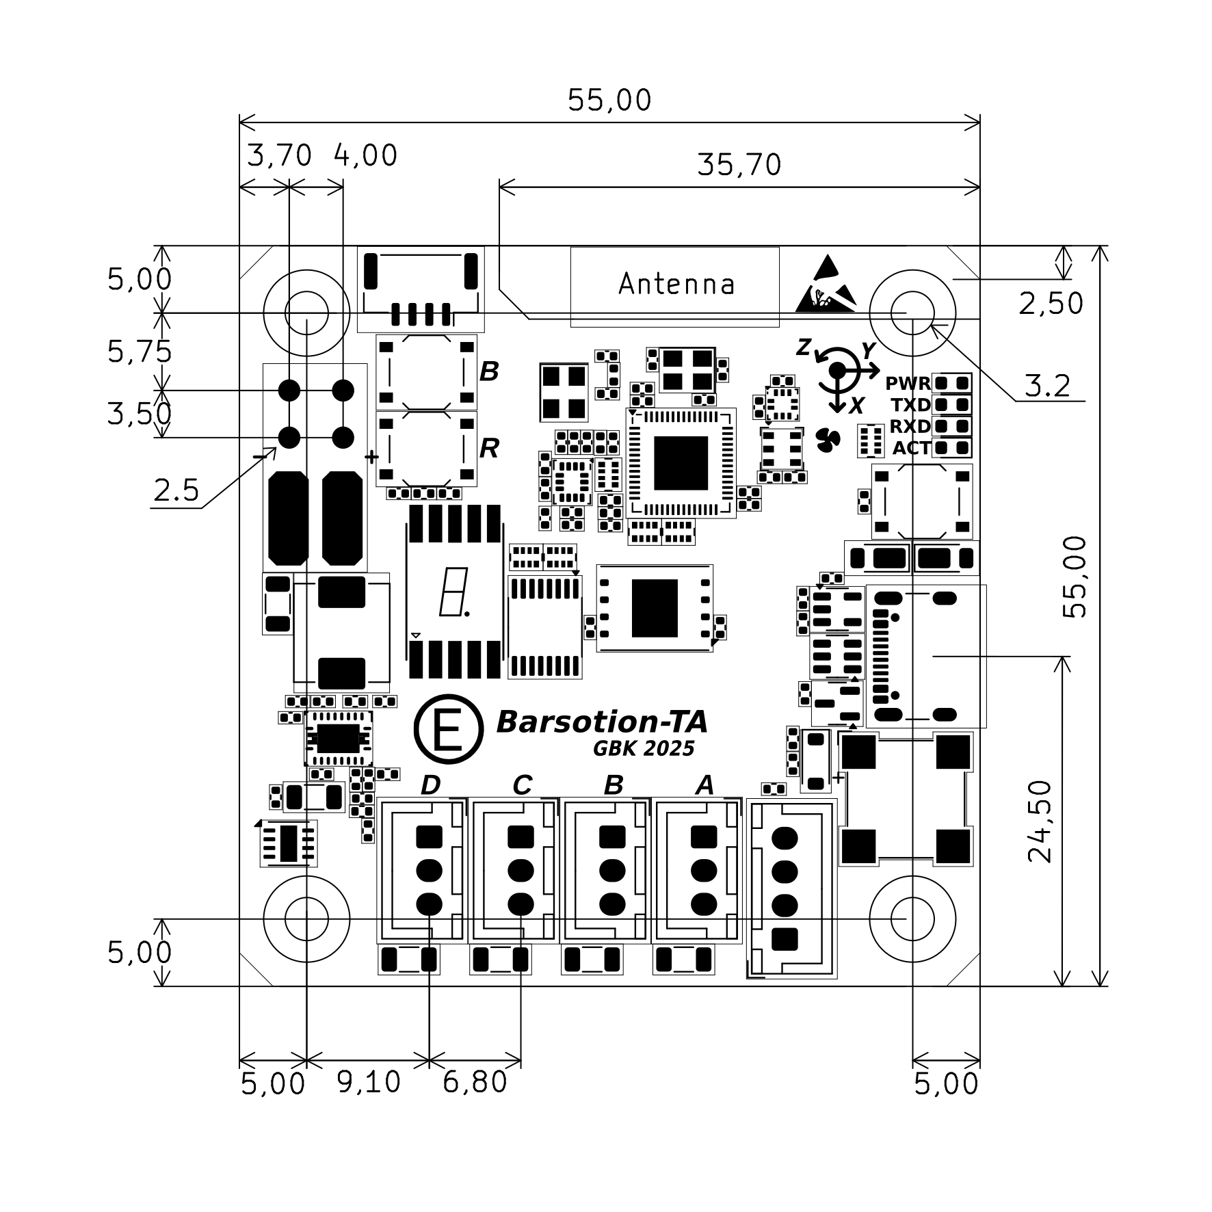
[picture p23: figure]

Figure 17: TA dimentions

### TA Structural schematic

The TA structural schematic is the same as for EA, but the 32.768 kHz quartz oscillator was added.


Figure 18: TA structural schematic

### TA Topology

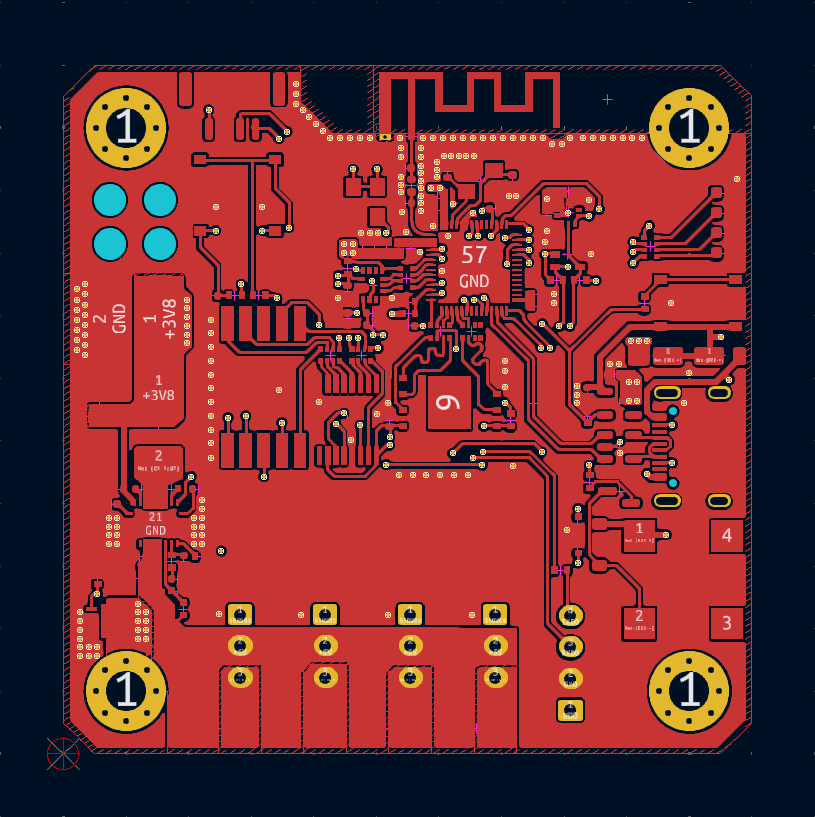
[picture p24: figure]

Figure 19: TA Layer 1 - Top signal

Figure 20: TA Layer 2 - GND

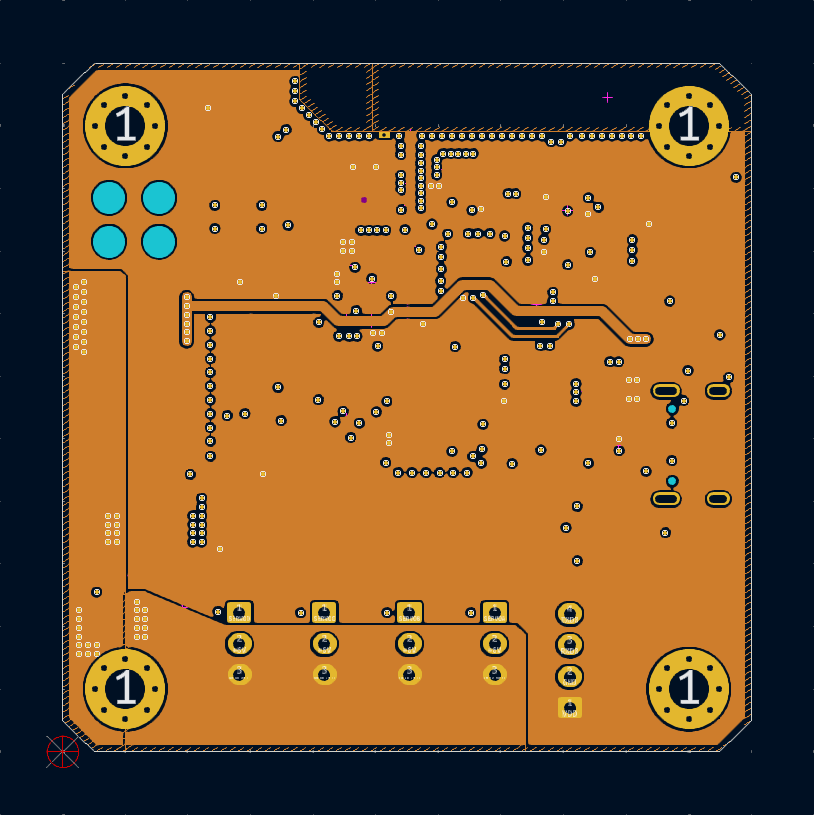
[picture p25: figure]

Figure 21: TA Layer 3 - Power

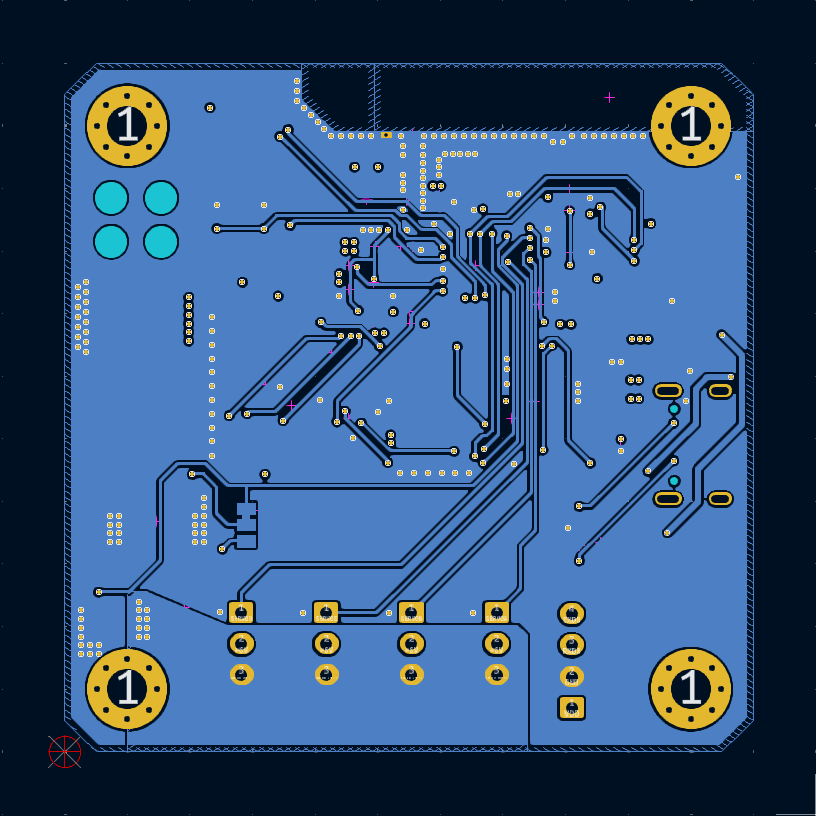
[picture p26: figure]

Figure 22: TA Layer 4 - Bottom signal

### TAv1.6 Topology

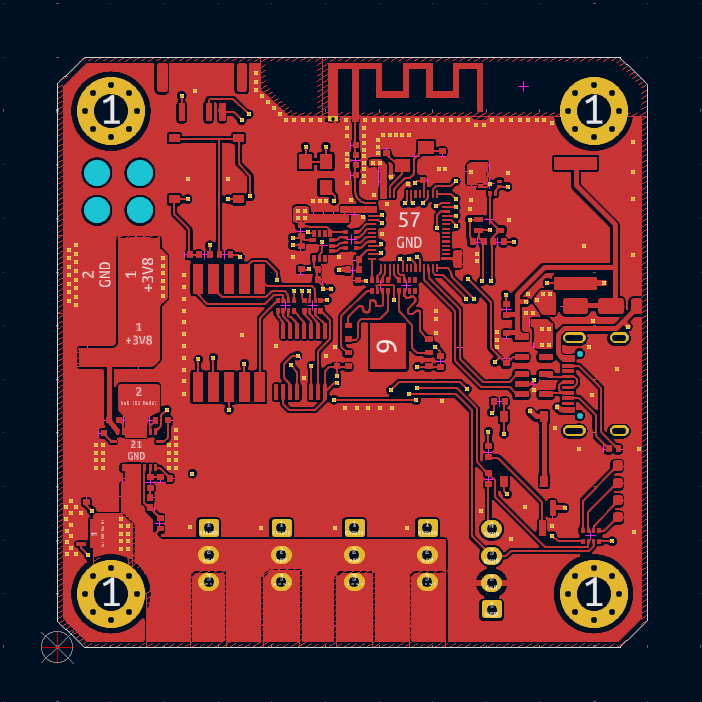
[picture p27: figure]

Figure 23: TAv1.6 Layer 1 - Top signal

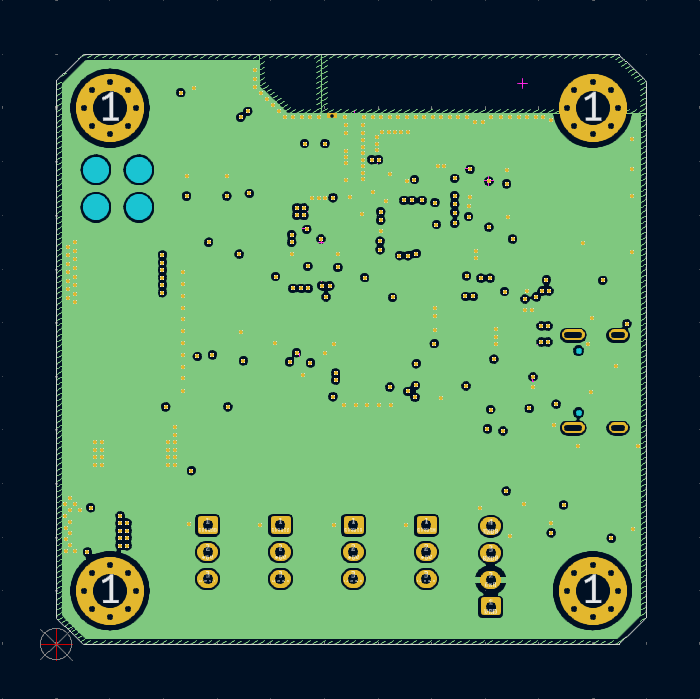
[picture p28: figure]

Figure 24: TAv1.6 Layer 2 - GND

Figure 25: TAv1.6 Layer 3 - Power

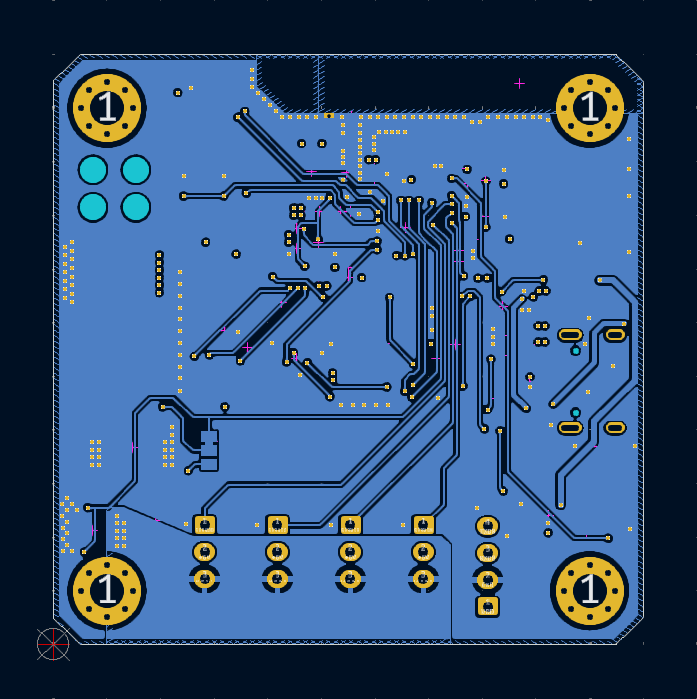
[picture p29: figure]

Figure 26: TAv1.6 Layer 4 - Bottom signal

### TA GitHub repository

Barsotion-TA’s KiCad sources, full schematic, pindefs-file are located at a project GitHub repository (https://github.com/Barsy-Barsevich/Barsotion-TA).

## EA & TA placing

The EA / TA board computer is placed in the nose rocket section as shown at the following renders.

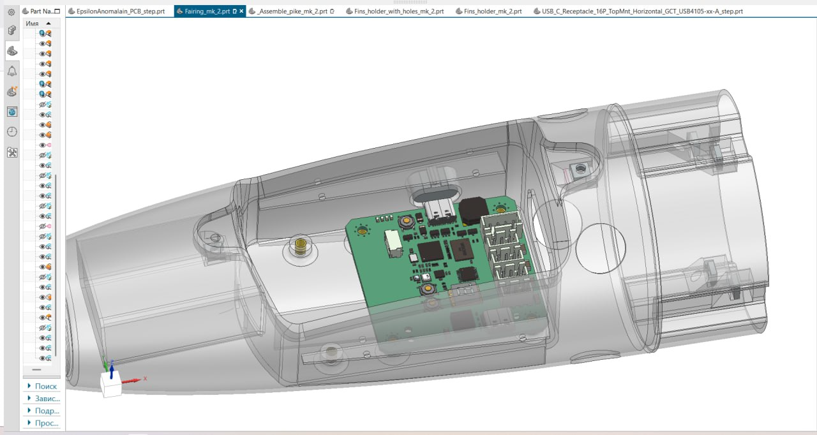
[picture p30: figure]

Figure 27: EA / TA placing

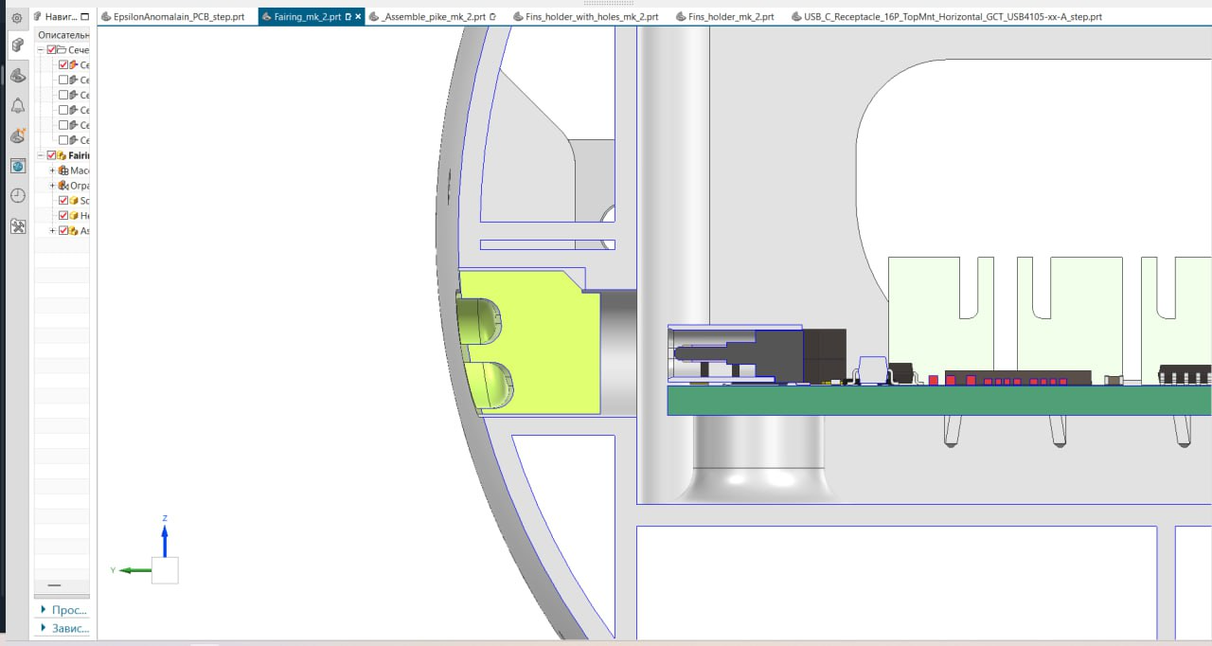
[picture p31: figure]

Figure 28: USB-C connector hole

## EA & TA software packet

### Abstract

The EA & TA software packet is a big complex software product. It is named after a modern philosopher A.Dugin.

### Device connection for flashing & communication

EA / TA device PC connection shown at figure. Only one USB-C cable is necessary for connection.

Software building & device flashing are proceeded via Espressif IDE (Eclipse-based). It is recommended to restart device in BOOT-mode before flashing (press “R” button on board when “B” button is pressed).

Communication with device is possible via serial terminal on PC or special command-line utility (see EA & TA PC interface).

Communication is proceeded via a set of ASCII-commands. It can be easily entered to serial terminal. The EA / TA device is ready to receive commands when it has sent a command line marker: “> “.

### Commands summary

Command | Description
Servo commands
SAP | SERVOA add a small positive offset (servo A bias plus)
SAM | SERVOA add a small negative offset (servo A bias minus)
SBP | SERVOB add a small positive offset (servo B bias plus)
SBM | SERVOB add a small negative offset (servo B bias minus)
SCP | SERVOC add a small positive offset (servo C bias plus)
SCM | SERVOC add a small negative offset (servo C bias minus)
SDP | SERVOD add a small positive offset (servo D bias plus)
SDM | SERVOD add a small negative offset (servo D bias minus)
SZERO | Reset zero offsets for all the servos and print
SPRINT | Print the servo angles (is needed if the servos were rotated manually and you need to check the zero-angles)
I2C commands
TWI-VERIFY | Check the connection of all the supported I2C peripherals
TWI-RESET | Reset the I2C bus
BMP388-ID | Get BMP388 ID and check it
AH3-ID | Get AH3 ID and check it
Disk commands
DISK-INFO | Print information about the disk: manufacturer, type, capacity, packet length, number of written packets, disk’s percent of usage
DISK-ERASE | Erase the disk. Checks the number of written packets and packet length, then erases the required amount of 128-KiB blocks
PACKET-WROTE | Prints the number of written packets
Get/set parameters commands
BOOT-ENTIRE-READ | Reads the disk’s boot entire and prints the information about entire encoding version, type of the device (EA or TA), device unique id, packet length, number of written packets, IMU calibration coefficients, IMU cycle frequency in Hz, token value (should be 0x55AA), etc.
PACKET-LEN | Prints the log packet length
IMU-CYCLE-FREQ | Get IMU cycle frequency in Hz
DEVICE | Get device’s info
SET-BOOT-ENTIRE | Set boot entire to default state
SET-IMU-CYCLE-FREQ | Set IMU cycle frequency in Hz (allowed values: 500, 1000, 2000, 4000, 8000)
IMU commands
IMU-CALIB | Calibrate IMU and save coefficients
IMU-CALIB-COEFS | Prints all the IMU calibration coefficients from boot entire
IMU-CALIB-EPSILON | Read IMU calibration parameter (epsilon)
SET-IMU-CALIB-EPSILON | Set IMU epsilon calibration parameter
System commands
POWER-OFF | Device power down
RESTART | Restart device
ACTION | Switches the computer to active mode
Helper commands
HELP | Prints available commands
Debug commands
PAGE-CONTENTS | Prints disk’s page contents
TEST-ACTION | Writes 1000 packets to the disk as is in Active mode and returns control to user’s terminal
TEST-ACTION-CYCLES | Get number of packet writing cycles for TEST-ACTION command
SET-TEST-ACTION-CYCLES | Sets number of packet writing cycles for TEST-ACTION command
Machine mode commands
MM-PACKET-LEN | Same as PACKET-LEN, but does not beepes at the end
MM-PACKET-WROTE | Same as PACKET-WROTE, but does not beepes at the end
MM-DISK-READ | Reading disk’s binary data

### Servo control commands

#### SxP & SxM commands

Created to calibrate servos zero state before flight. This commands, when received, add a small offset to the servo zero state and print zero state to the servos.

#### SZERO command

Resets all the extra offsets added by SxM & SxP commands and prints zero state value to servos.

#### SPRINT command

Prints zero state to the servos. It is needed if servos angles have already calibrated, but were changed manually so it is necessary to set calibrated zero state value to servos.

### I2C control commands

#### TWI-VERIFY command

Checks the BMP388 and AH3 connection and prints connection status to the serial.

#### TWI-RESET command

Figure 29: TWI-VERIFY command response

Resets the I2C bus. It is needed if the connection was lost but then.

#### BMP388-ID command

Reads BMP388’s ID and check it. The proper value is 0x50, if read value is not equal, the system raise the exception.

#### AH3-ID command

Figure 30: BMP388-ID command response

Reads AH3’s ID and check it. The proper value is 0x74, if read value is not equal, the system raise the exception.

### Disk control commands

Figure 31: AH3-ID command response

#### DISK-INFO command

Prints to the serial disk connection status, disk type (from JEDEC ID), capacity information, and if the boot entire is formatted, boot entire information: number of written packets, disk usage status.

#### DISK-ERASE command

Figure 32: DISK-INFO command response

Erases all the log area of disk. Erasing is necessary before writing information in Flash memory. DISK-ERASE command reads number of written packets and packet length values from boot entire and erases strictly necessary amount of blocks that save user’s time and device resource.

#### PACKET-WROTE command

Reads the number if written packets from the disk’s boot entire and prints it to the serial.

### Get/set parameters commands

#### BOOT-ENTIRE-READ command

Reads the boot entire and writes full information about if to the serial. It prints:

- Boot entire structure version (only 0x01 is today exists)
- Board type (EA or TA)
- Device unique ID (each board computer should have an unique number)
- Log packet length
- Number of written packets
- IMU calibration parameters

#### PACKET-LEN command

Figure 33: BOOT-ENTIRE-READ command response

Reads the packet length value from the disk’s boot entire and prints it to the serial.

#### IMU-CYCLE-FREQ command

Returns temporary defined IMU processing cycle frequency in Hz.

#### DEVICE command

Prints device’s info into the serial: device type (EA or TA) and device’s unique ID. The data are read from boot entire.

#### SET-BOOT-ENTIRE command

Figure 34: DEVICE command response

Sets boot entire to the default state:

- Sets the proper device according the software;
- Sets log packet size according the software;
- Sets number of written packets to zero;
- Sets IMU cycle frequency to 8000 Hz;
- Sets IMU calibration coefficients to zero;
- Sets number of packet writing cycles for TEST-ACTION to 1000;
- Sets token field to 0x55AA.

#### SET-IMU-CYCLE-FREQ command

Sets IMU cycle frequency. After the command input the interface asks user to text the frequency needed. Allowed values: “500”, “1000”, “2000”, “4000”, “8000”. If the user writes wrong value, the system terminates cycle frequency update and returns an error message.

Figure 35: SET-IMU-CYCLE-FREQ command response 1

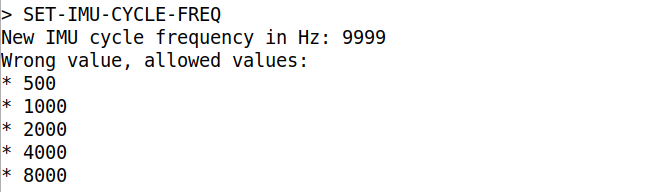
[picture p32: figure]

Figure 36: SET-IMU-CYCLE-FREQ command response 2

### IMU commands

#### IMU-CALIB command

Calibrates the IMU and writes calibration values to the disk.

#### IMU-CALIB-COEFS command

Prints calculated values read from the disk.

### System commands

Figure 37: IMU-CALIB-COEFS command response

#### POWER-OFF command

Power down the device. Note that the function does not work on EA.

#### RESTART command

Restarts the software.

#### ACTION command

Switch the device into the Active working mode.

### Helper commands

#### HELP command

Prints helper message with all the supported commands descriptions.

### Debug commands

#### PAGE-CONTENTS command

Prints page contents. After the user inputs this command, the system asks him, which page he would like to see. Then, after page number receiving, the system prints 2048 bytes of page contents in 16 columns with start addresses on the left hand.

#### TEST-ACTION command

Writes some packets to the disk. The command is created to simulate computer working in the Action mode. After packets writing, the system returns control to user.

#### TEST-ACTION-CYCLES

Reads number of packets that are to write while TEST-ACTION command processing.

#### SET-TEST-ACTION-CYCLES

Sets number of packets that are to write while TEST-ACTION command processing. The value is 1000 by default.

### Machine mode commands

#### MM-PACKET-LEN command

Does the same as PACKET-LEN, however it does not beeps the buzzer. This command is needed for EA & TA PC interface. “MM” means “machine mode”.

#### MM-PACKET-WROTE command

Does the same as PACKET-WROTE, however it does not beeps the buzzer. This command is needed for EA & TA PC interface.

#### MM-DISK-READ command

EA & TA board computers architecture allows to write a big amount of log data. When there are more than hundred megabytes of log data, their reading becomes a difficult task.

The Barsotion DeltaAnomalain board computer used to send log data to PC via serial interface as CSV-strings, so the packets were read, then converted to CSV-string and sent via UART.

This way was not effective because CSV-strings wear more than binary data. EA & TA software packet send packet data in binary form.

MM-DISK-READ command, when received, checks the disk connection and then responds OK, if the connection is valid. Then the board computer waits to sending any bytes via USB. When byte is sent, it sends a packet binary raw data as an answer. It sends packet 0 contents after start, then the address is incremented.

MM-DISK-READ command is used by EA & TA PC interface and allows read log data via USB at temporary maximum possible speed about 60 kilobytes per second.

## EA & TA PC interface

For the purpose of reading logs automatically and simplification EA & TA user experience, a gbk-oracle utility was created.

The log-decoder utility was created for decoding .bin file received as a result of gbk-oracle and conversion data to the JSON format.

### GBK Oracle utility

#### GBK Oracle usage

GBK Oracle utility needs the Python 3 installed on the PC.

The standard launch query look like as shown below.

Utility’s ‘--output-dir’ parameter is optional. It sets directory where the log file will be written. By default it is the same directory when program source file is located.

$ python3 gbk-oracle -p /dev/ttyACM0 --output-dir .

The ‘-p’ parameter defines serial port name. It is usually /dev/ttyACMx for Linux and COMx for Windows systems.

Optional ‘-b’ parameter sets the baudrate. It is maybe useless because USB interface do not mind about baudrate in CDC mode, data samples are transmitted by packets.

#### GBK Oracle commands

The GBK Oracle utility commands are mostly the same as EA & TA software packet serial interface commands, but there is a new command – DISK-READ.

GBK Oracle utility allows to enter commands . For example for command DISK-READ four writing forms are allowed

- DISK-READ
- DISK_READ
- disk-read
- disk_read

Then the full list of GBK Oracle commands is presented. In the following table ‘xxx-xxx’ form of commands is used in goal to separate GBK Oracle commands from EA & TA software packet commands.

Command | Description
sap | SERVOA add a small positive offset (servo A bias plus)
sam | SERVOA add a small negative offset (servo A bias minus)
sbp | SERVOB add a small positive offset (servo B bias plus)
sbm | SERVOB add a small negative offset (servo B bias minus)
scp | SERVOC add a small positive offset (servo C bias plus)
scm | SERVOC add a small negative offset (servo C bias minus)
sdp | SERVOD add a small positive offset (servo D bias plus)
sdm | SERVOD add a small negative offset (servo D bias minus)
szero | Reset zero offsets for all the servos and print
sprint | Print the servo angles (is needed if the servos were rotated manually and you need to check the zero-angles)
twi-verify | Check the connection of all the supported I2C peripherals
twi-reset | Reset the I2C bus
disk-info | Print information about the disk: manufacturer, type, capacity, packet len, number of written packets, disk’s percent of usage
disk-erase | Erase the disk. Checks the number of written packets and packet len, then erases the required amount of 128-kiB blocks
boot-entire-read | Reads the disk’s boot entire and prints the information about entire encoding version, type of the device (EA or TA), device unique id, packet length, number of written packets, imu calibration coefficients
packet-len | Prints the log packet len
packet-wrote | Prints the number of written packets
action | Switches the computer to active mode
power-off | Device power down
help | Prints available commands
disk-read | Reading disk’s data into the file
exit | Quit the program
quit | Quit the program

### Log decoder utility

#### Log decoder usage

The utility provides a simple usage. This string, sended to the bash terminal, decode log.bin file converting it to log.json.

$ python3 log-decoder --decoder-version 2

## Revision history

Date | Modification
May 8, 2025 | TAv1.6, new commands, Log decoder utility addidion
Apr 29, 2025 | Document creation

## Contacts

If you have any questions, feel free to write via email or Telegram.

Email: barsotion@yandex.ru

Telegram: @barsybarsevich

Barsotion EA & TA: User manual PRELIMINARY EDITION

PRELIMINARY EDITION

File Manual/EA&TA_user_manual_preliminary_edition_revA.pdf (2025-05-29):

## Barsotion EA & TA:

## User manual

### Table of contents

Barsotion EA & TA: User manual

Barsotion EA & TA: User manual

Barsotion EA & TA: User manual

### Overview

The EA & TA board computers as a part of Barsotion xAnomalain series are the devices created to control small model rockets flight and write down flight parameters. It was developed for the OKB “Iva” Pike rocket project.
These computers are the logical continuation of Barsotion GBK DeltaAnomalain board computer, used in OKB “Iva” Kilka project.
For the EA & TA developing, some radical principles were adopted:

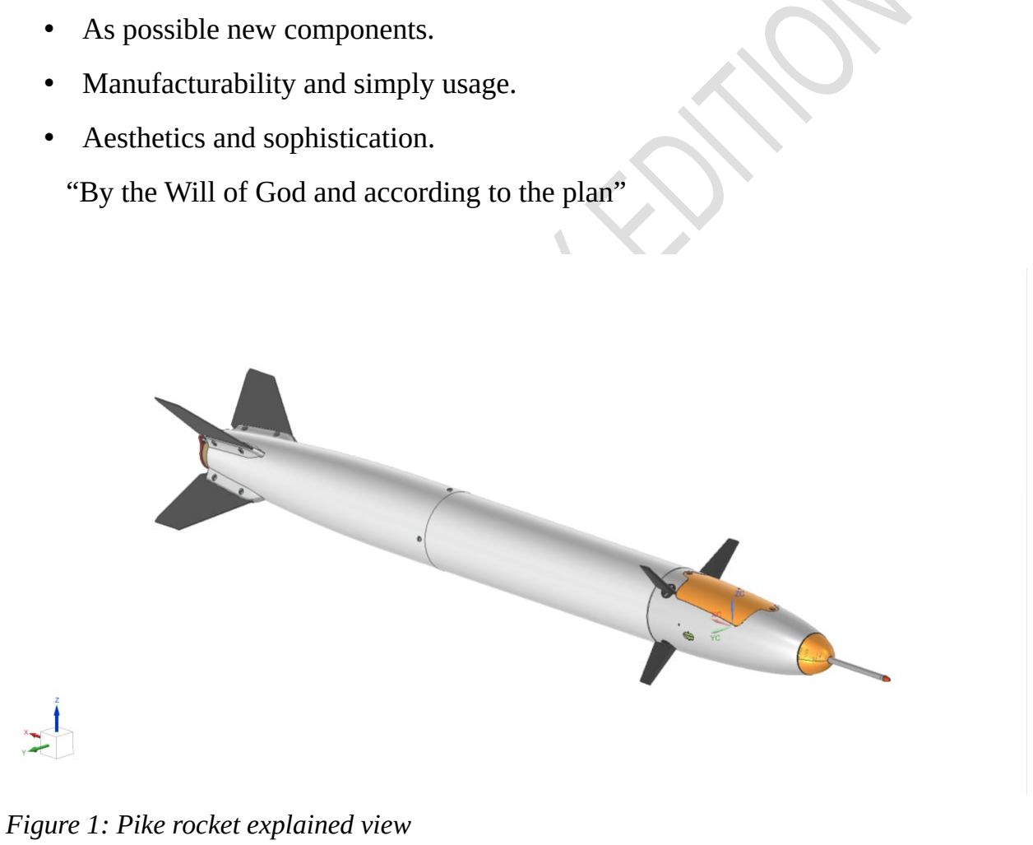
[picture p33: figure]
• As possible new components.; • Manufacturability and simply usage.; • Aesthetics and sophistication.; Figure 1: Pike rocket explained view

“By the Will of God and according to the plan”

4

Barsotion EA & TA: User manual

### EA hardware description

The Barsotion GBK EpsilonAnomalain boards (Barsotion-EA) was created as a part of model rocket project Pike.

EA Concepts
The Pike rocket has the following view:

The EA board computer (GBK) should be located at the nose of rocket, consist of one board and placed longitudinally. The power source is the 3.7 V 18650 battery with typical capacity around 3000 mA*h. The board computer should contain following sensors:
- Gyroscope & accelerometer (ICM-42688-P was chosen), connected via SPI, that is important because of necessity of ensuring high data read speed;
- Barometer (BMP388 was chosen);
- AH3 air speed sensor connector (4-pin, 3,3V, GND, SDA, SCL);
- Hygrometer (AHT20 was chosen).
The microcontroller should be enough rapid for processing gyroscope’s data a few thousand times per second. Reading data from the gyroscope should be synchronized with gyroscope’s interrupt channel.
Barometer and hygrometer data reading interrupt synchronization is not needed. The board computer should contain a flash memory chip, the capacity should not be less than 1 Gbit.
The board computer should have connectors for four MG90S servos. Also it should have a DC-DC boost voltage converter to provide servo feeding. The board

5

Figure 2: Pike rocket view

Barsotion EA & TA: User manual

computer should can power down servos if they are not used, because servos have a significant static power consumption.
The board computer should can measure battery voltage and have a power-off option, that allows to power down system by the microcontroller command.
The board computer should switch on by special button pressing. It is supposed that the computer will be connected to the battery a long time before the start so that long working not wanted. The computer should be switched on shortly before the start for saving the battery charge.
The computer should have a small seven-segment led indicator on the board for system status indication and also 4 LEDs:
- Power 3.3 V indication LED;
- TXD0 LED;
- RXD0 LED;
- User-driven LED.
The power indication helps to control the computer is working or not, TXD and RXD indication helps to control the data transmission progress. User-driven LED is needed for simplifying the debug process and improving the computer using user’s experience.
Also the board computer should have a buzzer that needed to signal when the rocked landed and waits to be found.

6

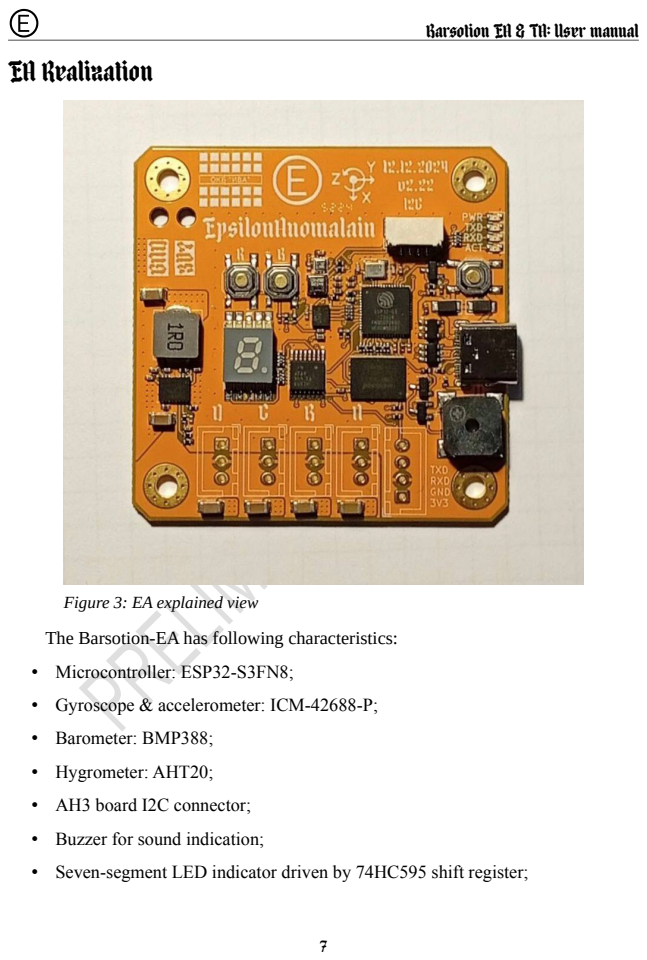
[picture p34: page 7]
EA Realization

Barsotion EA & TA: User manual

Figure 3: EA explained view
The Barsotion-EA has following characteristics:
• Microcontroller: ESP32-S3FN8;
• Gyroscope & accelerometer: ICM-42688-P;
• Barometer: BMP388;
• Hygrometer: AHT20;
• AH3 board I2C connector;
• Buzzer for sound indication;
• Seven-segment LED indicator driven by 74HC595 shift register;

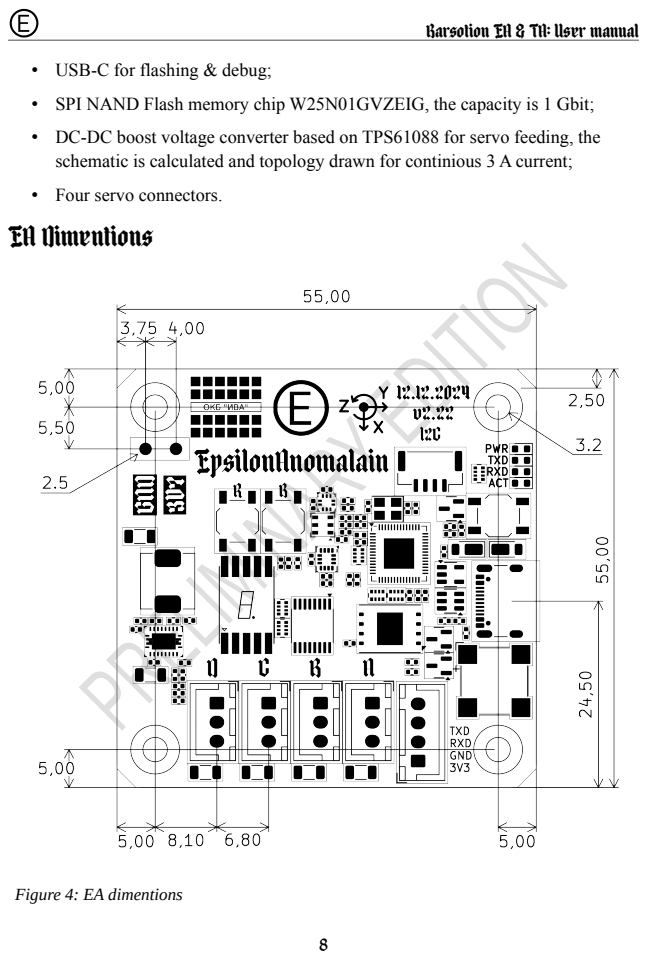
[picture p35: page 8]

Barsotion EA & TA: User manual

• USB-C for flashing & debug;
• SPI NAND Flash memory chip W25N01GVZEIG, the capacity is 1 Gbit;
• DC-DC boost voltage converter based on TPS61088 for servo feeding, the
schematic is calculated and topology drawn for continious 3 A current;
• Four servo connectors.
EA Dimentions

Figure 4: EA dimentions

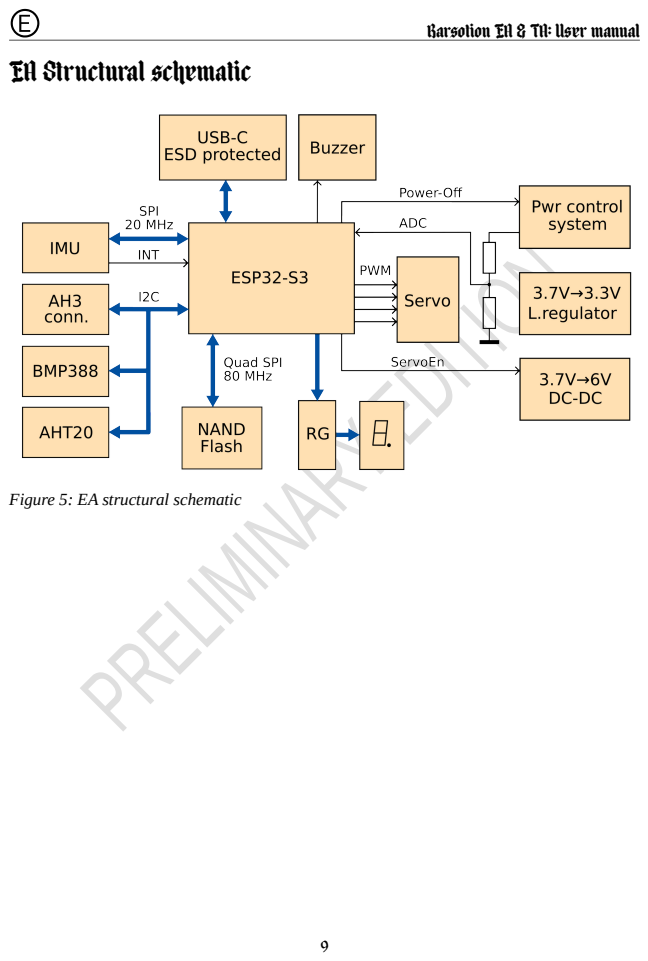
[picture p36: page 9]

Barsotion EA & TA: User manual

EA Structural schematic

Figure 5: EA structural schematic

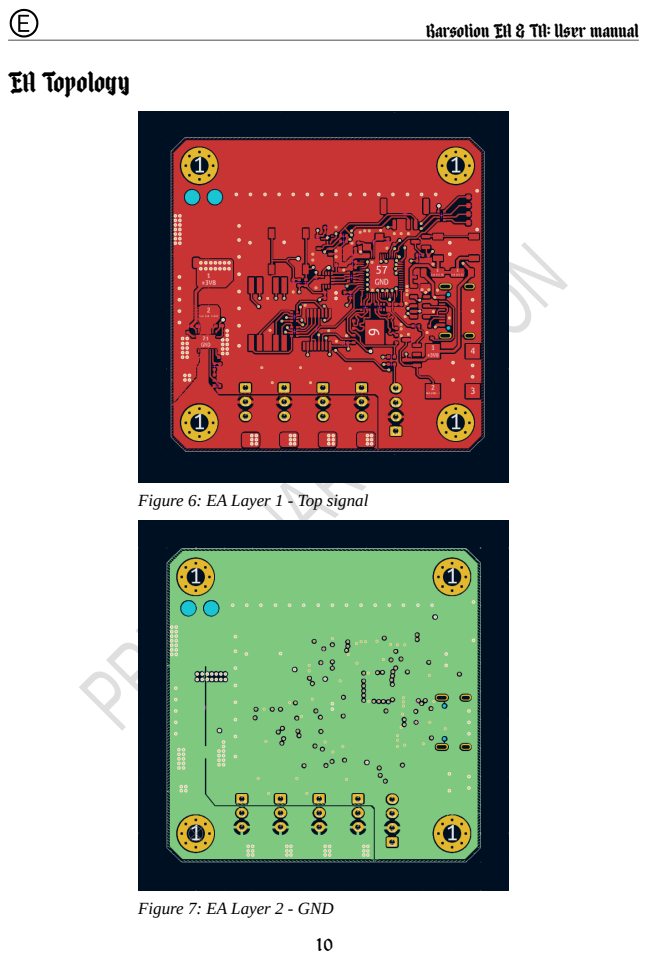
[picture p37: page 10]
EA Topology

Barsotion EA & TA: User manual

Figure 6: EA Layer 1 - Top signal

Figure 7: EA Layer 2 - GND

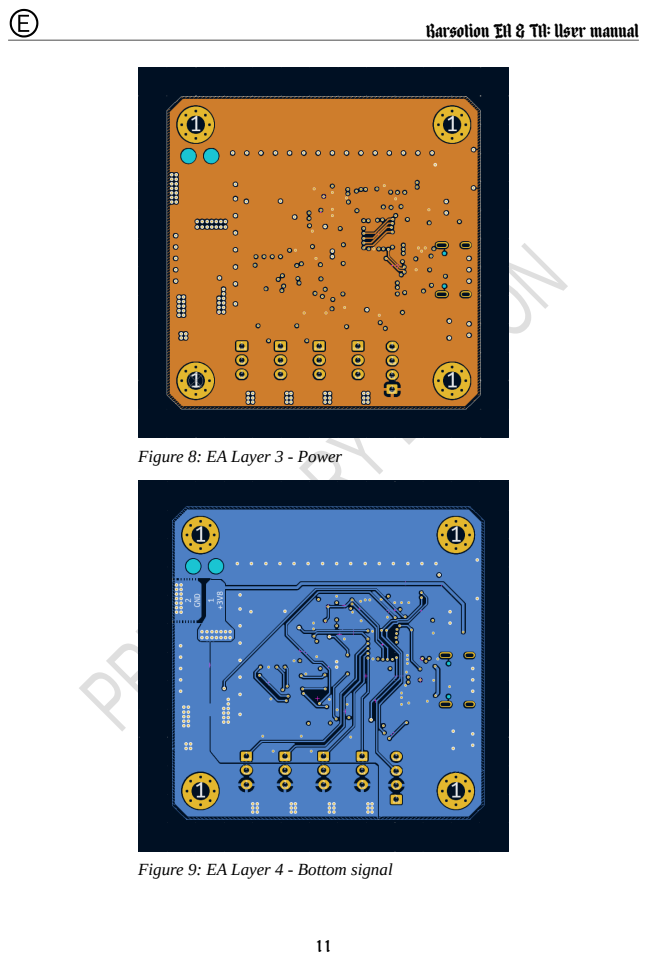
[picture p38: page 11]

Barsotion EA & TA: User manual

Figure 8: EA Layer 3 - Power

Figure 9: EA Layer 4 - Bottom signal

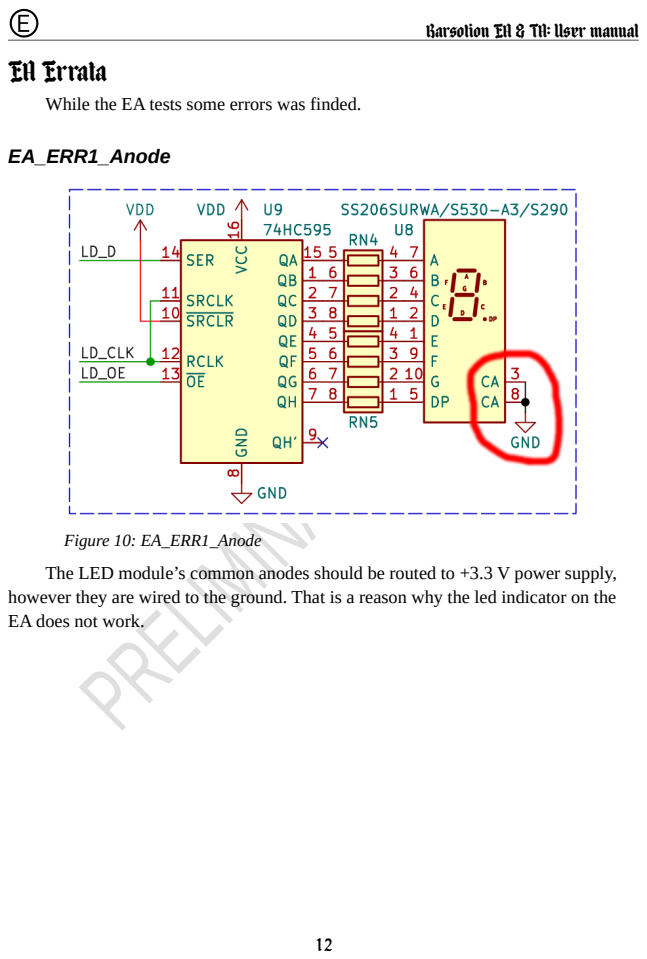
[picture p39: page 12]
EA_ERR1_Anode

Barsotion EA & TA: User manual

EA Errata
While the EA tests some errors was finded.

Figure 10: EA_ERR1_Anode
The LED module’s common anodes should be routed to +3.3 V power supply,
however they are wired to the ground. That is a reason why the led indicator on the
EA does not work.

Barsotion EA & TA: User manual

EA_ERR2_Poweroff

The EA boards have a hardware ability to power-off themselves by microcontroller command. It is useful if the battery voltage is low.
The power-off function does not work properly. When the OFF pin (GPIO38) is initialized as output and the logic 0 routed to this pin, the voltage on the VDD line decrease down to 1.8-1.9 V level, after that the GPIO block in the microcontroller stops the working, the OFF pin goes to tri-state condition, VDD capacitors’ residual charge provides a high level on the regulator’s EN pin and the device restarts.

13

Figure 11: EA_ERR2_Poweroff

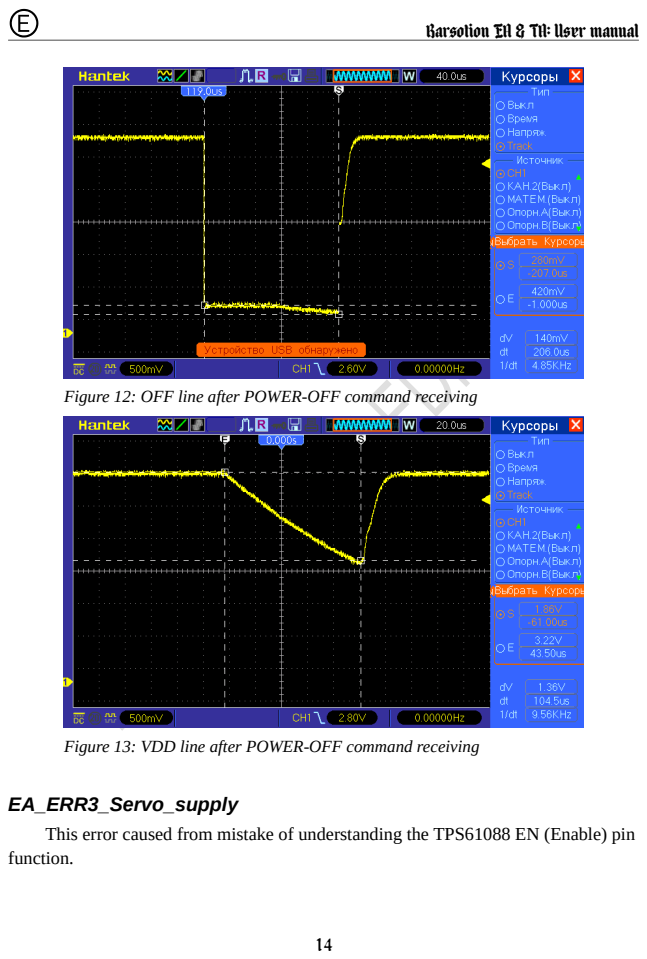
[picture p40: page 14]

Barsotion EA & TA: User manual

Figure 12: OFF line after POWER-OFF command receiving

Figure 13: VDD line after POWER-OFF command receiving

EA_ERR3_Servo_supply
This error caused from mistake of understanding the TPS61088 EN (Enable) pin
function.

Barsotion EA & TA: User manual

The SERVOEN line is wired directly from microcontroller to TPS61088’s EN pin. While the EA developing it means that if the EN pin is not active, there is no voltage on the 6 V output servo feeding line. However the EN pin only enables voltage conversion, not current passing by the converter IC.

EN pin enables driving the switch. If it is not active, switch is always unlocked, so the converter does not work. However the voltage still can pass through the inductor and diode to the servos. The solving of the problem is to add the transistor to the servo feeding circuit that can break the circuit if it is needed.

EA GitHub repository
Barsotion-EA’s KiCad sources, full schematic, pindefs-file are located at a project GitHub repository. (https://github.com/Barsy-Barsevich/Barsotion-EA)

15

Figure 14: Simplified boost converter circuit

Barsotion EA & TA: User manual

### TA hardware description

TA Concepts
The main goal of the TA creation is to fix the EA schematic error and problems. The most of device requirements are the same as for EA. However some extra features was wanted:
- Add the ICM-42688-P ODR frequency quartz stabilization
- Add 2.4 GHz WiFi / Bluetooth / BLE antenna
- Use 4 Gbit Flash chip instead of 1 Gbit
- Change the buzzer connection for allowing the buzzer to work when the board connected to the computer via USB (on the EA board the buzzer can make sound only if the battery connected)
According the EA&TA software architecture, the core 1’s cycle time depends on the ICM-42688-P INT1 pin period that is the same as the maximum of accelerometer & gyroscope’s ODRs. By default, the ODR frequency is generated from internal RC-source with 1% accuracy. Usual way to get the cycle time is considered in subtraction previous system timer’s value from actual. The ESP32-S3’s system timer has 1-microsecond accuracy, that does not allows to use ODR 16 kHz or 32 kHz because their periods have non-integer values in microseconds (62.5 & 31.25 microseconds), that causes bigger integral errors while integrating (the tests show that 8 kHz ODR gives smaller integral errors than 16 kHz, which contradicts the theory of numerical methods). The solving of the problem can be in ODR frequency quartz stabilization. If it is used, the ODR frequency has 10 ppm accuracy, so allows to use a constant as the cycle time value.
The 2.4 GHz antenna addition is not needed for rocket project tasks, however this requirement was added for getting more experience in high-frequency circuits topology design.
After the EA tests a curious fact was found: there are W25N01 memory chip pin-to-pin compatible chips with more capacity, for example W25N04. So using memory with more capacity is wanted.

16

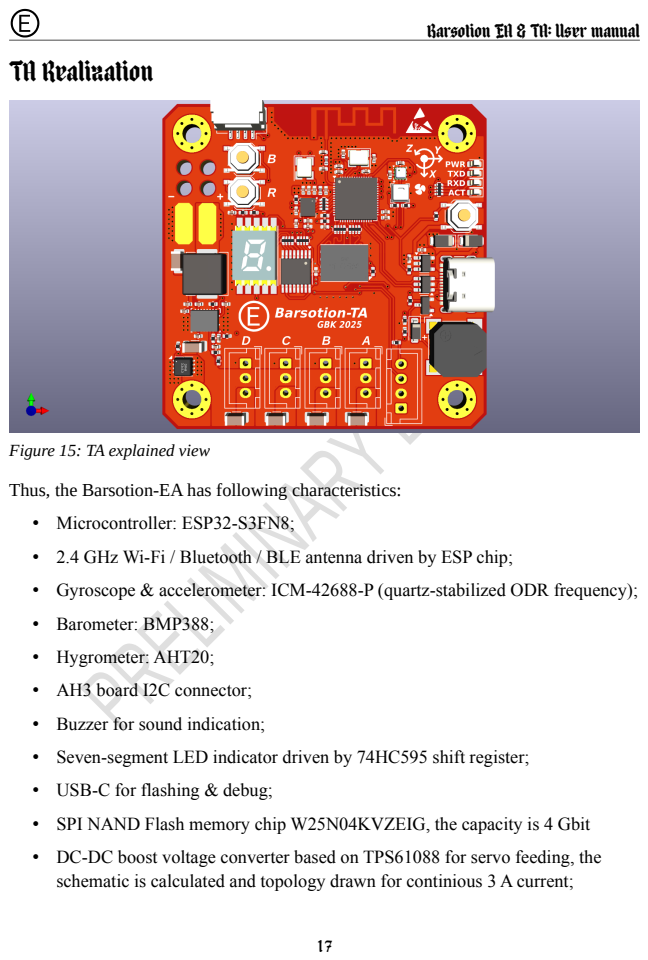
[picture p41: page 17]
TA Realization

Barsotion EA & TA: User manual

Figure 15: TA explained view

Thus, the Barsotion-EA has following characteristics:
• Microcontroller: ESP32-S3FN8;
• 2.4 GHz Wi-Fi / Bluetooth / BLE antenna driven by ESP chip;
• Gyroscope & accelerometer: ICM-42688-P (quartz-stabilized ODR frequency);
• Barometer: BMP388;
• Hygrometer: AHT20;
• AH3 board I2C connector;
• Buzzer for sound indication;
• Seven-segment LED indicator driven by 74HC595 shift register;
• USB-C for flashing & debug;
• SPI NAND Flash memory chip W25N04KVZEIG, the capacity is 4 Gbit
• DC-DC boost voltage converter based on TPS61088 for servo feeding, the
schematic is calculated and topology drawn for continious 3 A current;

Barsotion EA & TA: User manual

- Servo powerdown ability thanks to transistor breaking the feeding line;
- Four servo connectors.

TAv1.6
Because of BOM ambiguous interpretation a wrong buzzer was ordered, PKLCS1212E2000-R1 instead of CMT-8504-100-SMT-TR. The producing company agent told that they can deliver right buzzer, however CMT-8504-100-SMT-TR delivering takes two weeks that is much. Also, a schematic error was found in TA boards: wrong transistor Q2 connection caused by incorrect package pinout.

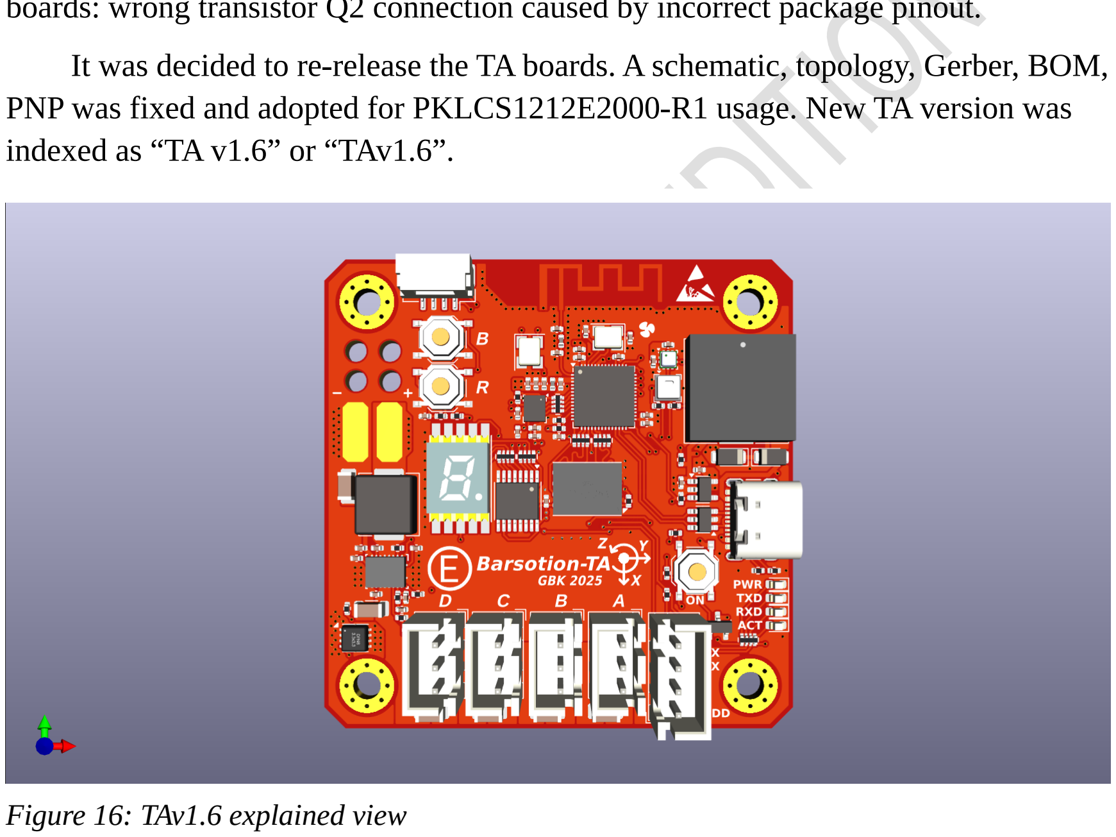
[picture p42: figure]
indexed as “TA v1.6” or “TAv1.6”.; Figure 16: TAv1.6 explained view

It was decided to re-release the TA boards. A schematic, topology, Gerber, BOM, PNP was fixed and adopted for PKLCS1212E2000-R1 usage. New TA version was

18

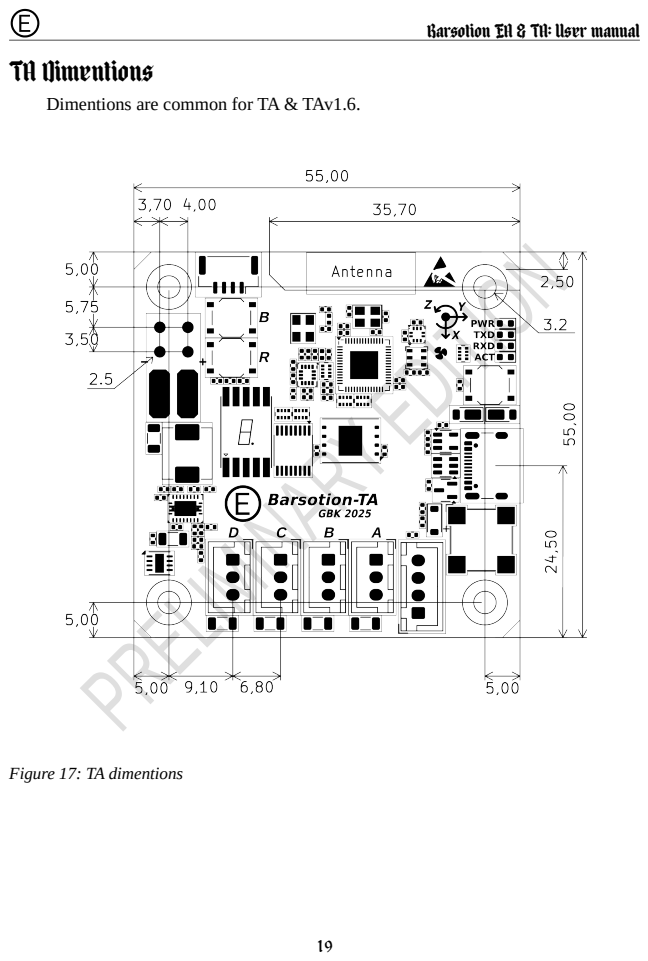
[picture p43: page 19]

Barsotion EA & TA: User manual

TA Dimentions
Dimentions are common for TA & TAv1.6.

Figure 17: TA dimentions

Barsotion EA & TA: User manual

TA Structural schematic
The TA structural schematic is the same as for EA, but the 32.768 kHz quartz
oscillator was added.

Figure 18: TA structural schematic

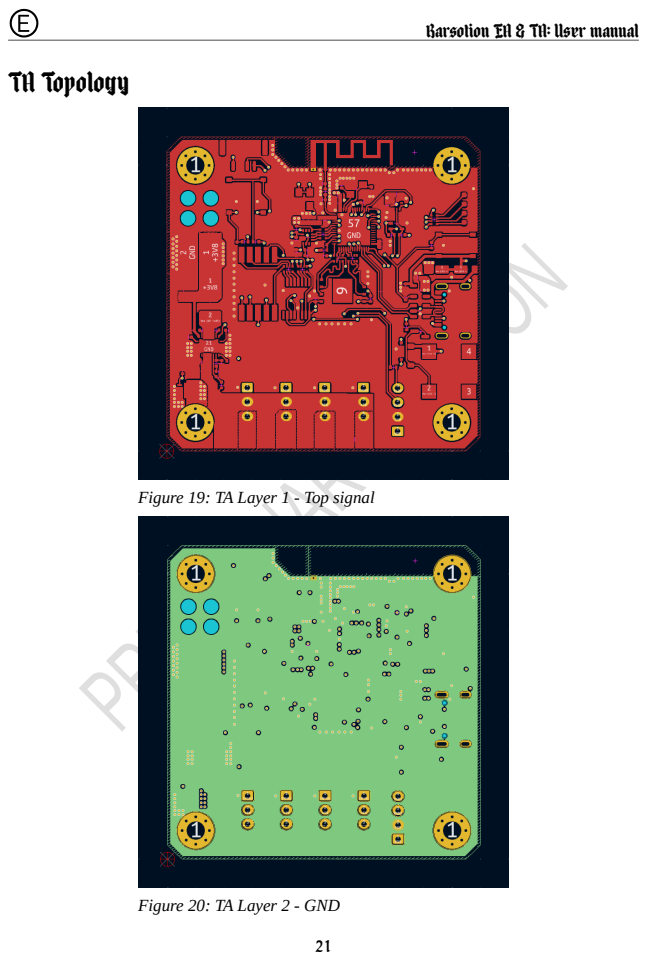
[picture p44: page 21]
TA Topology

Barsotion EA & TA: User manual

Figure 19: TA Layer 1 - Top signal

Figure 20: TA Layer 2 - GND

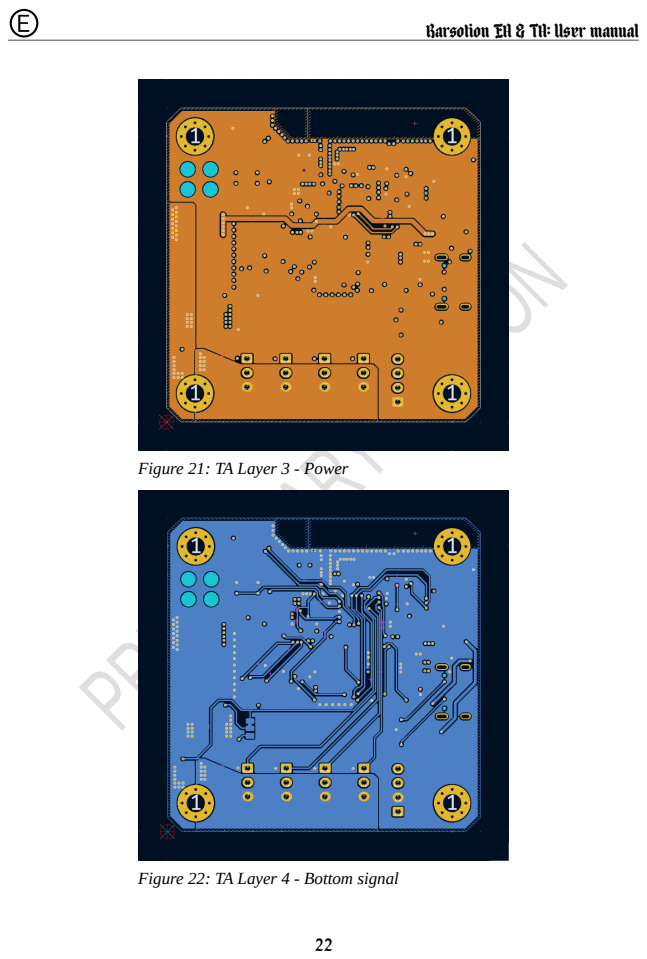
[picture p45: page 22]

Barsotion EA & TA: User manual

Figure 21: TA Layer 3 - Power

Figure 22: TA Layer 4 - Bottom signal

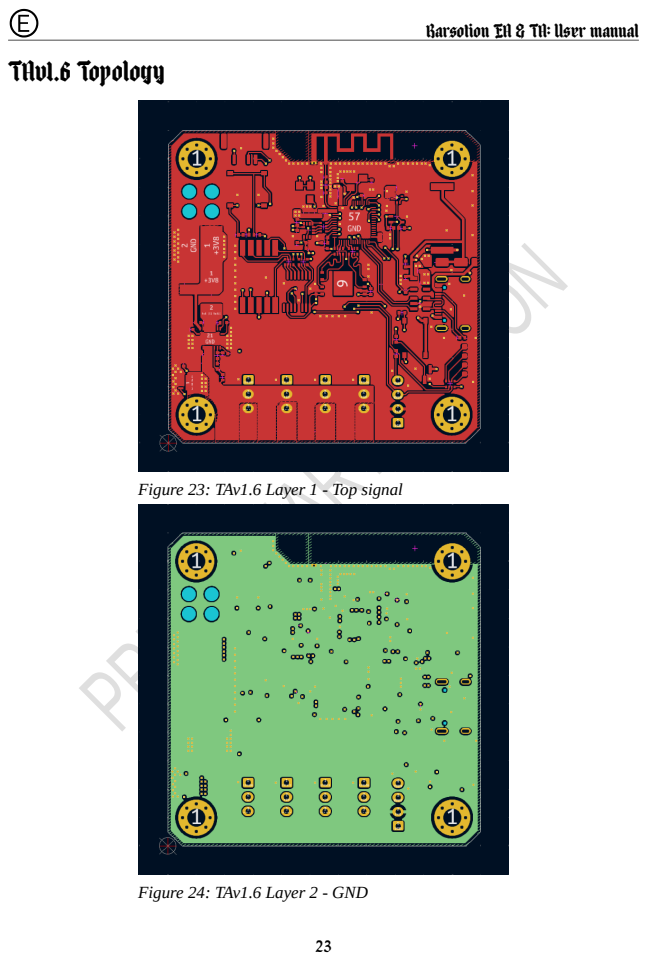
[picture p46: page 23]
TAv1.6 Topology

Barsotion EA & TA: User manual

Figure 23: TAv1.6 Layer 1 - Top signal

Figure 24: TAv1.6 Layer 2 - GND

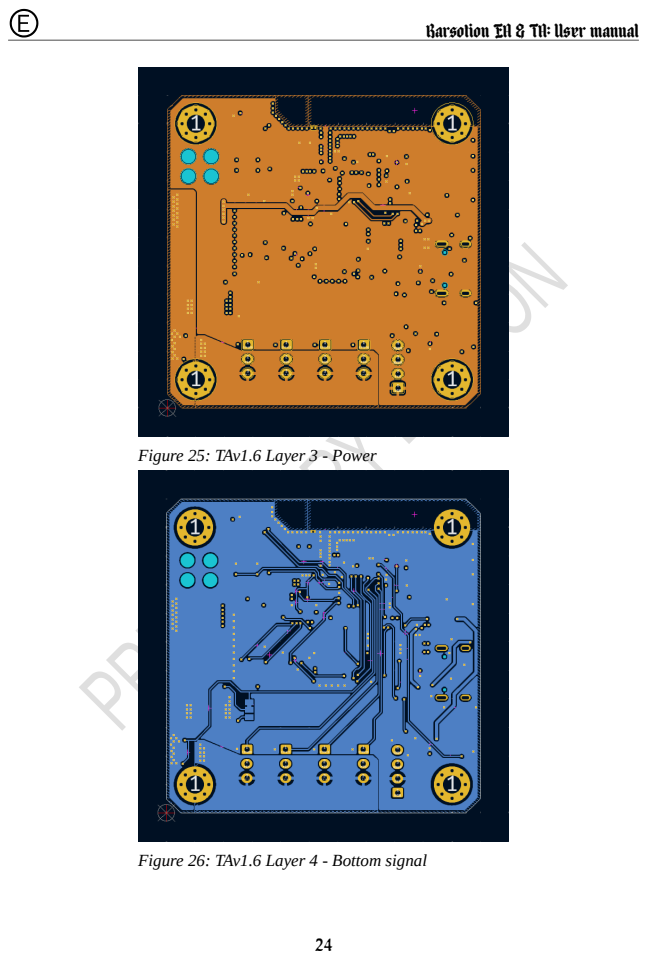
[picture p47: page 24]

Barsotion EA & TA: User manual

Figure 25: TAv1.6 Layer 3 - Power

Figure 26: TAv1.6 Layer 4 - Bottom signal

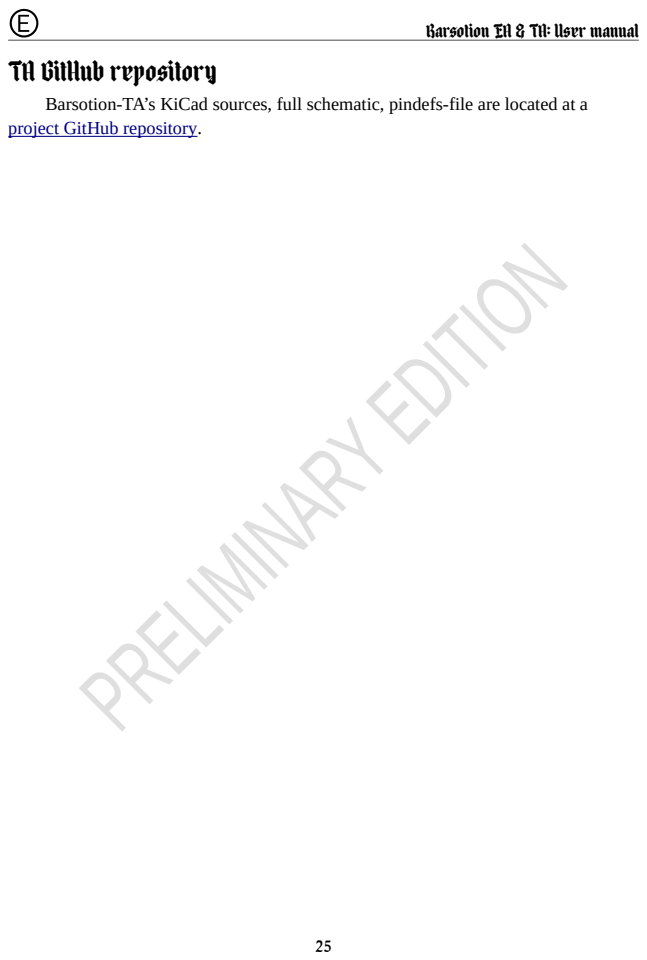
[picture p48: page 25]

Barsotion EA & TA: User manual

TA GitHub repository
Barsotion-TA’s KiCad sources, full schematic, pindefs-file are located at a
project GitHub repository. (https://github.com/Barsy-Barsevich/Barsotion-TA)

## EA & TA placing

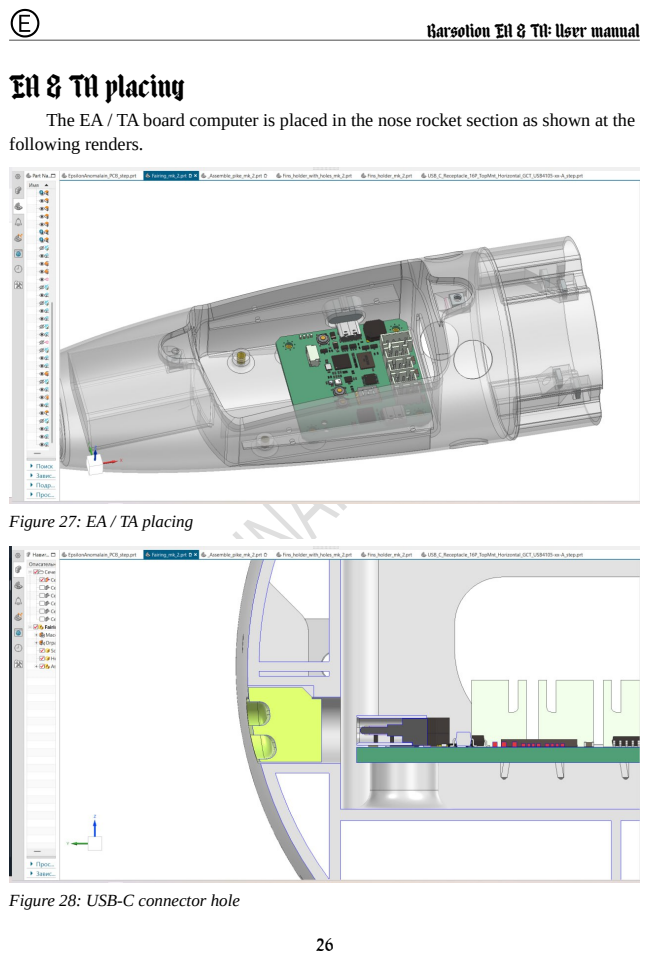
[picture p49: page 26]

Barsotion EA & TA: User manual

The EA / TA board computer is placed in the nose rocket section as shown at the
following renders.

Figure 27: EA / TA placing

Figure 28: USB-C connector hole

Barsotion EA & TA: User manual

### EA & TA software packet

Abstract
The EA & TA software packet is a big complex software product. It is named after a modern philosopher A.Dugin.

Device connection for flashing & communication
EA / TA device PC connection shown at figure. Only one USB-C cable is necessary for connection.
Software building & device flashing are proceeded via Espressif IDE (Eclipse-based). It is recommended to restart device in BOOT-mode before flashing (press “R” button on board when “B” button is pressed).
Communication with device is possible via serial terminal on PC or special command-line utility (see EA & TA PC interface).
Communication is proceeded via a set of ASCII-commands. It can be easily entered to serial terminal. The EA / TA device is ready to receive commands when it has sent a command line marker: “> “.

Commands summary
Command | Description
Servo commands
SAP | SERVOA add a small positive offset (servo A bias plus)
SAM | SERVOA add a small negative offset (servo A bias minus)
SBP | SERVOB add a small positive offset (servo B bias plus)
SBM | SERVOB add a small negative offset (servo B bias minus)
SCP | SERVOC add a small positive offset (servo C bias plus)
SCM | SERVOC add a small negative offset (servo C bias minus)
SDP | SERVOD add a small positive offset (servo D bias plus)
SDM | SERVOD add a small negative offset (servo D bias minus)
SZERO | Reset zero offsets for all the servos and print
SPRINT | Print the servo angles (is needed if the servos were rotated
| 27

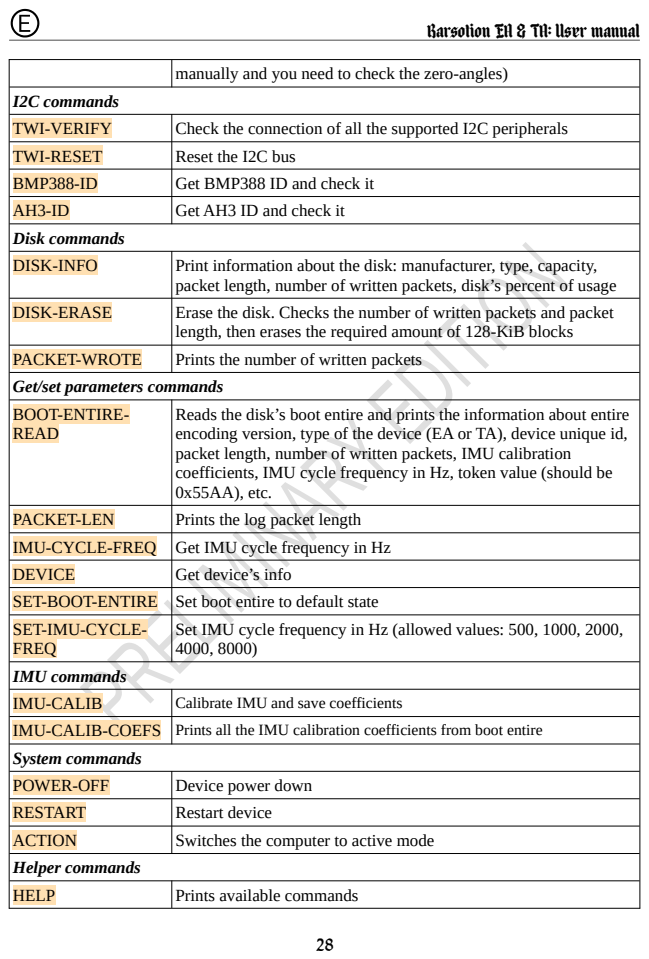
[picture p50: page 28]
I2C commands; Disk commands; IMU commands; System commands; Helper commands; HELP; Prints available commands

Barsotion EA & TA: User manual

manually and you need to check the zero-angles)

TWI-VERIFY | Check the connection of all the supported I2C peripherals
TWI-RESET | Reset the I2C bus
BMP388-ID | Get BMP388 ID and check it
AH3-ID | Get AH3 ID and check it

DISK-INFO | Print information about the disk: manufacturer, type, capacity, packet length, number of written packets, disk’s percent of usage

DISK-ERASE | Erase the disk. Checks the number of written packets and packet length, then erases the required amount of 128-KiB blocks

PACKET-WROTE | Prints the number of written packets

Get/set parameters commands

BOOT-ENTIRE-READ | Reads the disk’s boot entire and prints the information about entire encoding version, type of the device (EA or TA), device unique id, packet length, number of written packets, IMU calibration coefficients, IMU cycle frequency in Hz, token value (should be 0x55AA), etc.

PACKET-LEN | Prints the log packet length
IMU-CYCLE-FREQ | Get IMU cycle frequency in Hz
DEVICE | Get device’s info
SET-BOOT-ENTIRE | Set boot entire to default state
SET-IMU-CYCLE-FREQ | Set IMU cycle frequency in Hz (allowed values: 500, 1000, 2000, 4000, 8000)

IMU-CALIB | Calibrate IMU and save coefficients
IMU-CALIB-COEFS | Prints all the IMU calibration coefficients from boot entire

POWER-OFF | Device power down
RESTART | Restart device
ACTION | Switches the computer to active mode

Barsotion EA & TA: User manual

Debug commands
PAGE-CONTENTS | Prints disk’s page contents
TEST-ACTION | Writes 1000 packets to the disk as is in Active mode and returns control to user’s terminal

Machine mode commands
MM-PACKET-LEN | Same as PACKET-LEN, but does not beepes at the end
MM-PACKET- WROTE | Same as PACKET-WROTE, but does not beepes at the end
MM-DISK-READ | Reading disk’s binary data

Servo control commands

SxP & SxM commands
Created to calibrate servos zero state before flight. This commands, when received, add a small offset to the servo zero state and print zero state to the servos.

SZERO command
Resets all the extra offsets added by SxM & SxP commands and prints zero state value to servos.

SPRINT command
Prints zero state to the servos. It is needed if servos angles have already calibrated, but were changed manually so it is necessary to set calibrated zero state value to servos.

I2C control commands

TWI-VERIFY command
Checks the BMP388 and AH3 connection and prints connection status to the serial.

29


Barsotion EA & TA: User manual

Figure 29: TWI-VERIFY command response

TWI-RESET command
Resets the I2C bus. It is needed if the connection was lost but then.

BMP388-ID command
Reads BMP388’s ID and check it. The proper value is 0x50, if read value is not
equal, the system raise the exception.

Figure 30: BMP388-ID command response

AH3-ID command
Reads AH3’s ID and check it. The proper value is 0x74, if read value is not

Barsotion EA & TA: User manual

Disk control commands

DISK-INFO command
Prints to the serial disk connection status, disk type (from JEDEC ID), capacity information, and if the boot entire is formatted, boot entire information: number of written packets, disk usage status.

DISK-ERASE command
Erases all the log area of disk. Erasing is necessary before writing information in Flash memory. DISK-ERASE command reads number of written packets and packet length values from boot entire and erases strictly necessary amount of blocks that save user’s time and device resource.

PACKET-WROTE command
Reads the number if written packets from the disk’s boot entire and prints it to the serial.

Get/set parameters commands

BOOT-ENTIRE-READ command
Reads the boot entire and writes full information about if to the serial. It prints:
- Boot entire structure version (only 0x01 is today exists)

31

Figure 32: DISK-INFO command response

Figure 31: AH3-ID command response

Barsotion EA & TA: User manual

- Board type (EA or TA)
- Device unique ID (each board computer should have an unique number)
- Log packet length

• Number of written packets; • IMU calibration parameters; PACKET-LEN command; serial.; IMU-CYCLE-FREQ command; DEVICE command

Reads the packet length value from the disk’s boot entire and prints it to the

Returns temporary defined IMU processing cycle frequency in Hz.

Prints device’s info into the serial: device type (EA or TA) and device’s unique ID. The data are read from boot entire.

32

Figure 33: BOOT-ENTIRE-READ command response

Barsotion EA & TA: User manual

SET-BOOT-ENTIRE command
Sets boot entire to the default state:
- Sets the proper device according the software;
- Sets log packet size according the software;
- Sets number of written packets to zero;
- Sets IMU cycle frequency to 8000 Hz;
- Sets IMU calibration coefficients to zero;
- Sets token field to 0x55AA.

SET-IMU-CYCLE-FREQ command
Sets IMU cycle frequency. After the command input the interface asks user to text the frequency needed. Allowed values: “500”, “1000”, “2000”, “4000”, “8000”. If the user writes wrong value, the system terminates cycle frequency update and returns an error message.


33

Figure 35: SET-IMU-CYCLE-FREQ command response 1

Figure 36: SET-IMU-CYCLE-FREQ command response 2

Figure 34: DEVICE command response

IMU commands; System commands

Barsotion EA & TA: User manual

IMU-CALIB command
Calibrates the IMU and writes calibration values to the disk.

IMU-CALIB-COEFS command
Prints calculated values read from the disk.

Figure 37: IMU-CALIB-COEFS command response

POWER-OFF command
Power down the device. Note that the function does not work on EA.

RESTART command
Restarts the software.

ACTION command
Switch the device into the Active working mode.
Helper commands

HELP command
Prints helper message with all the supported commands descriptions.

Barsotion EA & TA: User manual
Debug commands

PAGE-CONTENTS command
Prints page contents. After the user inputs this command, the system asks him, which page he would like to see. Then, after page number receiving, the system prints 2048 bytes of page contents in 16 columns with start addresses on the left hand.

TEST-ACTION command
Writes 1000 packets to the disk. The command is created to simulate computer working in the Action mode. After packets writing, the system returns control to user.

Machine mode commands

MM-PACKET-LEN command
Does the same as PACKET-LEN, however it does not beeps the buzzer. This command is needed for EA & TA PC interface. “MM” means “machine mode”.

MM-PACKET-WROTE command
Does the same as PACKET-WROTE, however it does not beeps the buzzer. This command is needed for EA & TA PC interface.

MM-DISK-READ command
EA & TA board computers architecture allows to write a big amount of log data. When there are more than hundred megabytes of log data, their reading becomes a difficult task.
The Barsotion DeltaAnomalain board computer used to send log data to PC via serial interface as CSV-strings, so the packets were read, then converted to CSV-string and sent via UART.
This way was not effective because CSV-strings wear more than binary data. EA & TA software packet send packet data in binary form.
MM-DISK-READ command, when received, checks the disk connection and then responds OK, if the connection is valid. Then the board computer waits to

35

Barsotion EA & TA: User manual

sending any bytes via USB. When byte is sent, it sends a packet binary raw data as an answer. It sends packet 0 contents after start, then the address is incremented. MM-DISK-READ command is used by EA & TA PC interface and allows read log data via USB at temporary maximum possible speed about 60 kilobytes per second.


36

Barsotion EA & TA: User manual

## EA & TA PC interface

For the purpose of reading logs automatically and simplification EA & TA user experience, a gbk-oracle utility was created.
The log-decoder utility was created for decoding .bin file received as a result of gbk-oracle and conversion data to the JSON format.

### GBK Oracle utility

GBK Oracle usage
GBK Oracle utility needs the Python 3 installed on the PC. The standard launch query look like as shown below.

Utility’s ‘--output-dir’ parameter is optional. It sets directory where the log file will be written. By default it is the same directory when program source file is located.
The ‘-p’ parameter defines serial port name. It is usually /dev/ttyACMx for Linux and COMx for Windows systems.
Optional ‘-b’ parameter sets the baudrate. It is maybe useless because USB interface do not mind about baudrate in CDC mode, data samples are transmitted by packets.

GBK Oracle commands
The GBK Oracle utility commands are mostly the same as EA & TA software packet serial interface commands, but there is a new command – DISK-READ. GBK Oracle utility allows to enter commands . For example for command DISK-READ four writing forms are allowed
- DISK-READ
- DISK_READ

37

$ python3 gbk-oracle -p /dev/ttyACM0 --output-dir .

Barsotion EA & TA: User manual

- disk-read
- disk_read
Then the full list of GBK Oracle commands is presented. In the following table ‘xxx-xxx’ form of commands is used in goal to separate GBK Oracle commands from EA & TA software packet commands.
Command | Description
sap | SERVOA add a small positive offset (servo A bias plus)
sam | SERVOA add a small negative offset (servo A bias minus)
sbp | SERVOB add a small positive offset (servo B bias plus)
sbm | SERVOB add a small negative offset (servo B bias minus)
scp | SERVOC add a small positive offset (servo C bias plus)
scm | SERVOC add a small negative offset (servo C bias minus)
sdp | SERVOD add a small positive offset (servo D bias plus)
sdm | SERVOD add a small negative offset (servo D bias minus)
szero | Reset zero offsets for all the servos and print
sprint | Print the servo angles (is needed if the servos were rotated manually and you need to check the zero-angles)
twi-verify | Check the connection of all the supported I2C peripherals
twi-reset | Reset the I2C bus
disk-info | Print information about the disk: manufacturer, type, capacity, packet len, number of written packets, disk’s percent of usage
disk-erase | Erase the disk. Checks the number of written packets and packet len, then erases the required amount of 128-kiB blocks
boot-entire-read | Reads the disk’s boot entire and prints the information about entire encoding version, type of the device (EA or TA), device unique id, packet length, number of written packets, imu calibration coefficients
packet-len | Prints the log packet len
packet-wrote | Prints the number of written packets
action | Switches the computer to active mode
power-off | Device power down
help | Prints available commands
| 38

disk-read; Reading disk’s data into the file; exit; Quit the program; quit

Barsotion EA & TA: User manual

Log decoder utility

Log decoder usage

$ python3 log-decoder --decoder-version 2

The utility provides a simple usage. This string, sended to the bash terminal,
decode log.bin file converting it to log.json.

### Revision history

Barsotion EA & TA: User manual

Date | Modification
May 8, 2025 | TAv1.6, new commands, Log decoder utility addidion
Apr 29, 2025 | Document creation

### Contacts

Barsotion EA & TA: User manual

If you have any questions, feel free to write via email or Telegram.
Email: barsotion@yandex.ru
Telegram: @barsybarsevich

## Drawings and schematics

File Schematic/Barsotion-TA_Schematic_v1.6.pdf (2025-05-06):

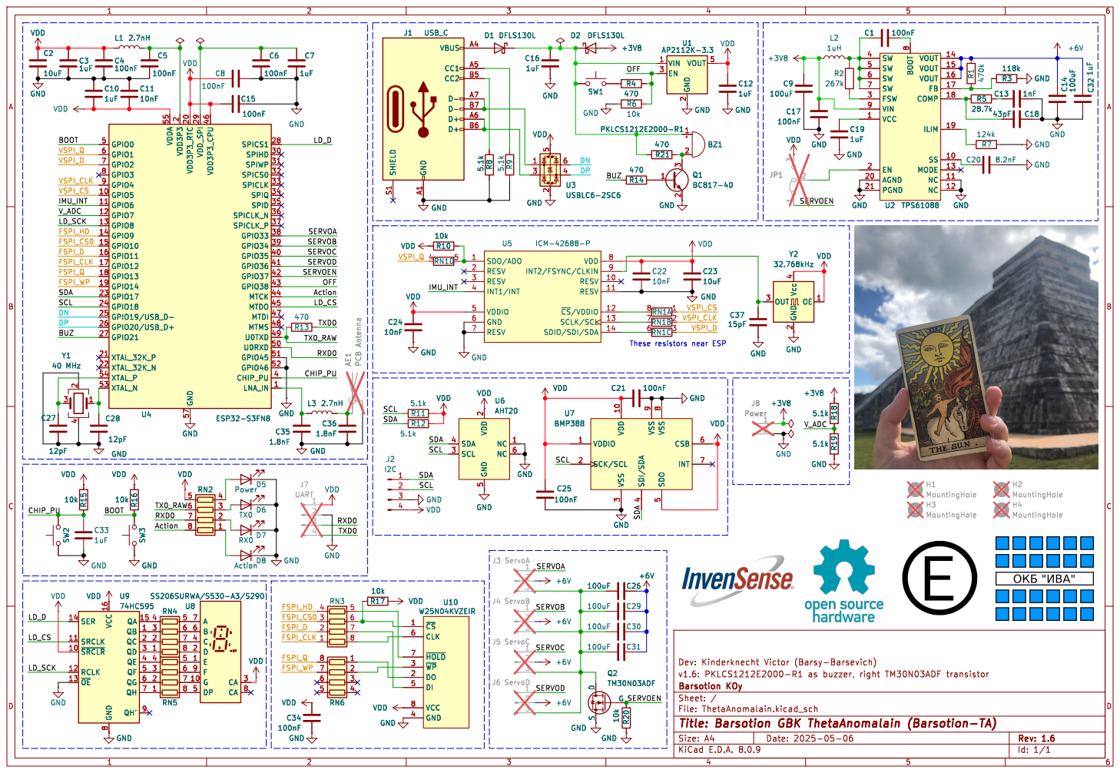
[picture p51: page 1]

2 EN 3 VOUT 5 U1 AP2112K-3.3 GND GND

2 VDD3P3_RTC 20 XTAL_32K_P 21 XTAL_32K_N 22 GPIO17 23 GPIO18 24 GPIO19/USB_D- 25 GPIO20/USB_D+ 26 GPIO21 27 SPICS1 28 VDD_SPI 29 SPIHD 30 SPIWP 31 SPICS0 32 SPICLK 33 SPIQ 34 SPID 35 SPICLK_P 37 GPIO33 38 GPIO34 39 CHIP_PU 4 GPIO35 40 GPIO36 41 GPIO37 42 GPIO38 43 MTCK 44 VDD3P3_CPU 46 MTDI 47 MTMS 48 U0TXD 49 GPIO0 5 U0RXD 50 GPIO46 52 XTAL_N 53 XTAL_P 54 VDDA 55 GND 57 GPIO1 6 GPIO2 7 GPIO3 8 GPIO4 9 Y1

2 VDD3P3_RTC 20 XTAL_32K_P 21 XTAL_32K_N 22 GPIO17 23 GPIO18 24 GPIO19/USB_D- 25 GPIO20/USB_D+ 26 GPIO21 27 SPICS1 28 VDD_SPI 29 SPIHD 30 SPIWP 31 SPICS0 32 SPICLK 33 SPIQ 34 SPID 35 SPICLK_P 37 GPIO33 38 GPIO34 39 CHIP_PU 4 GPIO35 40 GPIO36 41 GPIO37 42 GPIO38 43 MTCK 44 VDD3P3_CPU 46 MTDI 47 MTMS 48 U0TXD 49 GPIO0 5 U0RXD 50 GPIO46 52 XTAL_N 53 XTAL_P 54 VDDA 55 GND 57 GPIO1 6 GPIO2 7 GPIO3 8 GPIO4 9 U4 ESP32-S3FN8 GND R18 5.1k R19 5.1k GND

S GND R20 10k GND GND GND

2 OUT 3 Vcc 4 GND GND

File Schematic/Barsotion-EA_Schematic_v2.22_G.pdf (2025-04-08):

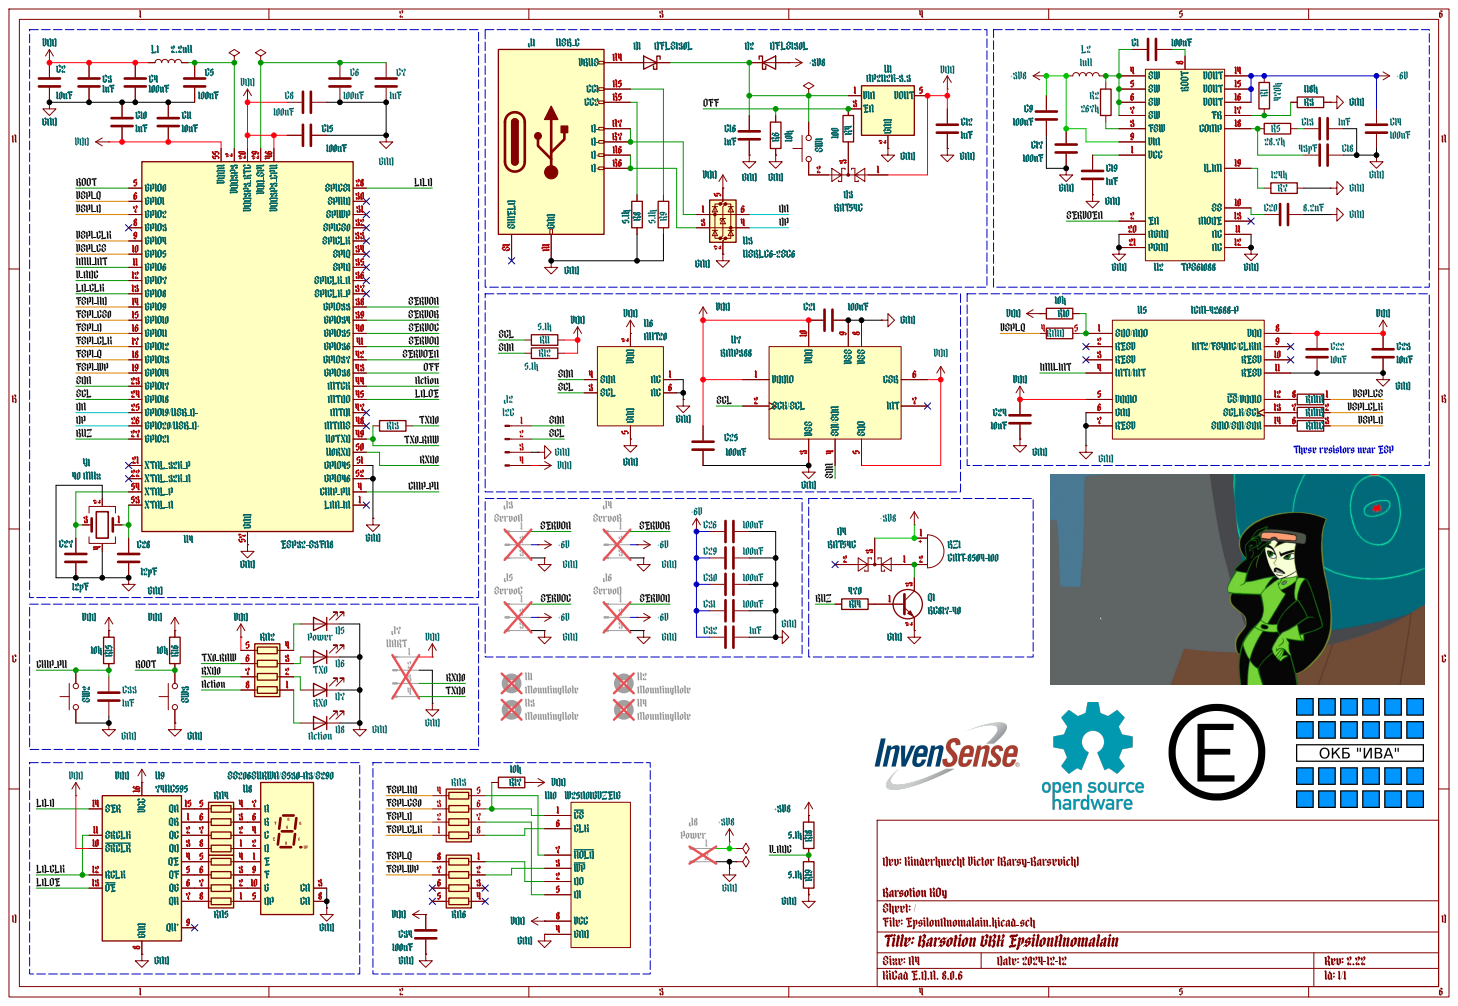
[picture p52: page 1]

2 EN 3 VOUT5 U1 AP2112K-3.3 GND GND R4 100 SW1 GND

8 VIN 9 GND GND GND

2 VDD3P3_RTC20 XTAL_32K_P 21 XTAL_32K_N 22 GPIO17 23 GPIO18 24 GPIO19/USB_D- 25 GPIO20/USB_D+ 26 GPIO21 27 SPICS128 VDD_SPI29 SPIHD30 SPIWP31 SPICS032 SPICLK33 SPIQ34 SPID35 SPICLK_P37 GPIO3338 GPIO3439 CHIP_PU4 GPIO3540 GPIO3641 GPIO3742 GPIO3843 MTCK 44 VDD3P3_CPU46 MTDI 47 MTMS 48 U0TXD49 GPIO0 5 U0RXD50 GPIO4652 XTAL_N 53 XTAL_P 54 VDDA55 GND 57 GPIO1 6 GPIO2 7 GPIO3 8 GPIO4 9 U4 ESP32-S3FN8 C10

2 VDD3P3_RTC20 XTAL_32K_P 21 XTAL_32K_N 22 GPIO17 23 GPIO18 24 GPIO19/USB_D- 25 GPIO20/USB_D+ 26 GPIO21 27 SPICS128 VDD_SPI29 SPIHD30 SPIWP31 SPICS032 SPICLK33 SPIQ34 SPID35 SPICLK_P37 GPIO3338 GPIO3439 CHIP_PU4 GPIO3540 GPIO3641 GPIO3742 GPIO3843 MTCK 44 VDD3P3_CPU46 MTDI 47 MTMS 48 U0TXD49 GPIO0 5 U0RXD50 GPIO4652 XTAL_N 53 XTAL_P 54 VDDA55 GND 57 GPIO1 6 GPIO2 7 GPIO3 8 GPIO4 9C10

Theseresistors near ESP GND

File: EpsilonAnomalain.kicad_sch Sheet:/ BarsotionKOy Dev:KinderknechtVictor (Barsy-Barsevich) 1

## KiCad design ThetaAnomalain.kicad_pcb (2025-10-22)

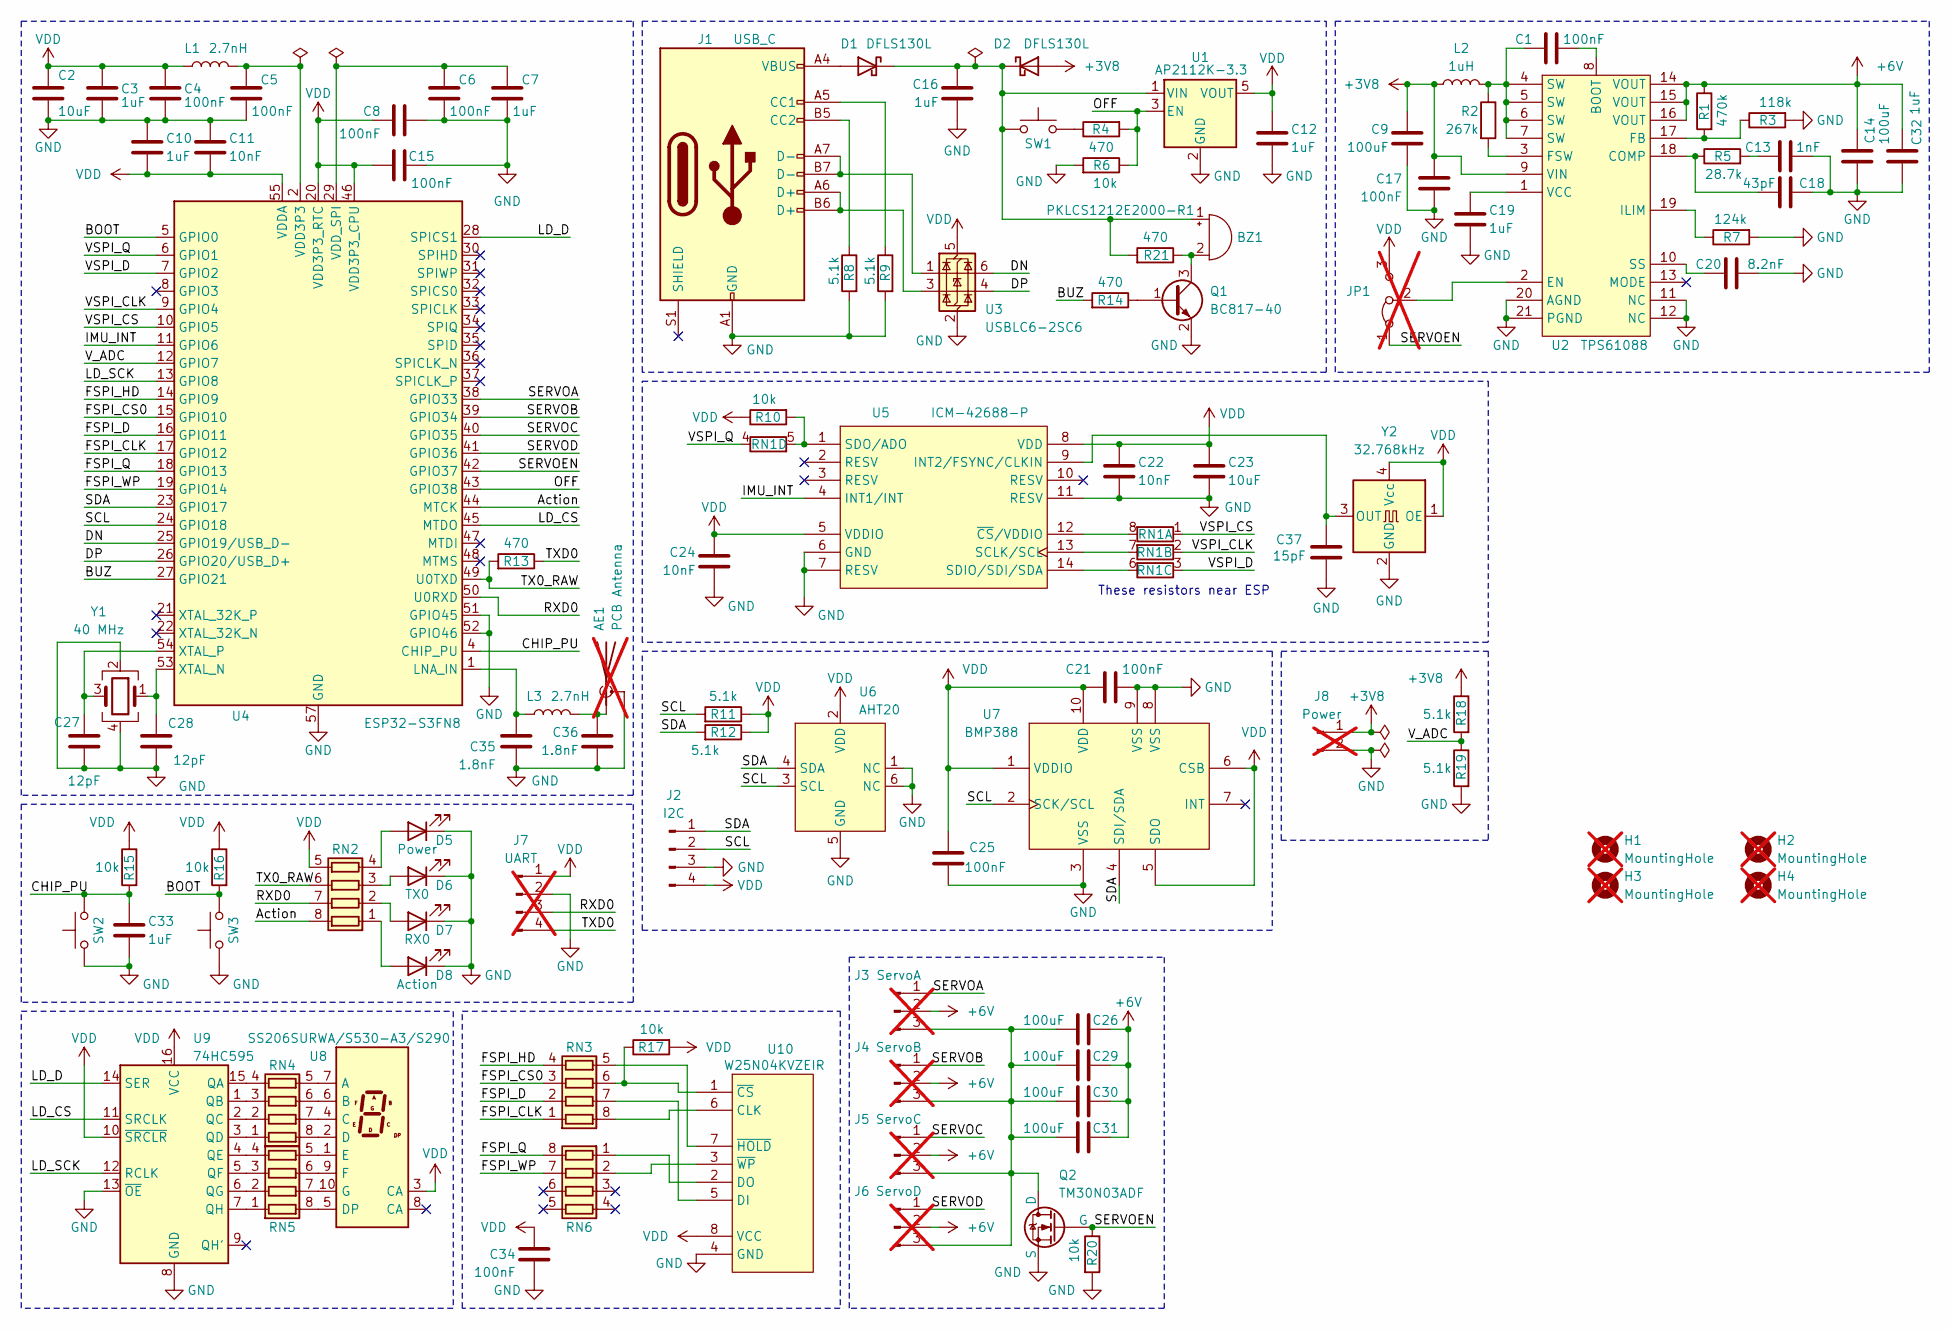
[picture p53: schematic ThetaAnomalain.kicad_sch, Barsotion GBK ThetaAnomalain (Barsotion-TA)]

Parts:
AE1: PCB Antenna; Texas_SWRA117D_2.4GHz_Right; not fitted
BZ1: PKLCS1212E2000-R1; Buzzer_Murata_PKLCS1212E; Mfr.Part PKLCS1212E2000-R1
C1, C4, C5, C6, C8, C15, C17, C21, C25, C34: 100nF; C_0402_1005Metric
C2, C23: 10uF; C_0402_1005Metric
C3, C7, C10, C12, C16, C19, C32, C33: 1uF; C_0402_1005Metric
C9, C14, C26, C29, C30, C31: 100uF; C_1206_3216Metric
C11, C22, C24: 10nF; C_0402_1005Metric
C13: 1nF; C_0402_1005Metric
C18: 43pF; C_0402_1005Metric
C20: 8.2nF; C_0402_1005Metric
C27, C28: 12pF; C_0402_1005Metric
C35, C36: 1.8nF; C_0402_1005Metric
C37: 15pF; C_0402_1005Metric
D1, D2: DFLS130L; D_PowerDI-123
D5: Power; LED_0603_1608Metric; Mfr.Part TJ-S1608CY6T5ALC9Y-A5
D6: TX0; LED_0603_1608Metric; Mfr.Part TJ-S1608CY6T5ALC9Y-A5
D7: RX0; LED_0603_1608Metric; Mfr.Part TJ-S1608CY6T5ALC9Y-A5
D8: Action; LED_0603_1608Metric; Mfr.Part TJ-S1608CY6T5ALC9Y-A5
H1, H2, H3, H4: MountingHole; MountingHole_3.2mm_M3_Pad_Via; not fitted
J1: USB_C; USB_C_Receptacle_GCT_USB4105-xx-A_16P_TopMnt_Horizontal; Mfr.Part TYPE C-DB-116PWB
J2: I2C; JST_GH_SM04B-GHS-TB_1x04-1MP_P1.25mm_Horizontal; Mfr.Part A1257WR-S-4P
J3: ServoA; JST_XH_B3B-XH-A_1x03_P2.50mm_Vertical; not fitted
J4: ServoB; JST_XH_B3B-XH-A_1x03_P2.50mm_Vertical; not fitted
J5: ServoC; JST_XH_B3B-XH-A_1x03_P2.50mm_Vertical; not fitted
J6: ServoD; JST_XH_B3B-XH-A_1x03_P2.50mm_Vertical; not fitted
J7: UART; JST_XH_B4B-XH-A_1x04_P2.50mm_Vertical; not fitted
J8: Power; Battery_3V7_Cable_connector_v2; not fitted
JP1: Jumper_3_Bridged12; SolderJumper-3_P1.3mm_Bridged12_Pad1.0x1.5mm_NumberLabels; not fitted
L1, L3: 2.7nH; L_0402_1005Metric
L2: 1uH; L_APV_APH0630; Mfr.Part APH0630T1R0M
Q1: BC817-40; SOT-23
Q2: TM30N03ADF; PDFN3x3-8L; Mfr.Part TM30N03ADF
R1: 470k; R_0402_1005Metric
R2: 267k; R_0402_1005Metric
R3: 118k; R_0402_1005Metric
R4, R13, R14, R21: 470; R_0402_1005Metric
R5: 28.7k; R_0402_1005Metric
R6, R10, R15, R16, R17, R20: 10k; R_0402_1005Metric
R7: 124k; R_0402_1005Metric
R8, R9, R11, R12, R18, R19: 5.1k; R_0402_1005Metric
RN1: 47; R_Array_Convex_4x0402
RN2, RN4, RN5: 1k; R_Array_Convex_4x0402
RN3, RN6: 0; R_Array_Convex_4x0402
SW1, SW2, SW3: TS-1187A-B-A-B; SW_Push_1P1T_XKB_TS-1187A; Mfr.Part TS-1187A-B-A-B
U1: AP2112K-3.3; SOT-23-5; Mfr.Part AP2112K-3.3TRG1
U2: TPS61088; RHL0020A; Mfr.Part TPS61088RHLR
U3: USBLC6-2SC6; SOT-23-6; Mfr.Part USBLC6-2SC6
U4: ESP32-S3FN8; QFN-56-1EP_7x7mm_P0.4mm_EP4x4mm; Mfr.Part ESP32-S3FN8
U5: ICM-42688-P; LGA-14_3x2.5mm_P0.5mm_LayoutBorder3x4y; Mfr.Part ICM-42688-P
U6: AHT20; Mfr.Part AHT20
U7: BMP388; BMP388_v2; Mfr.Part BMP388
U8: SS206SURWA/S530-A3/S290; SS206SURWA; Mfr.Part SS206SURWA/S530-A3/S290
U9: 74HC595; TSSOP-16_4.4x5mm_P0.65mm; Mfr.Part SN74HC595PWR
U10: W25N04KVZEIR; WSON-8-1EP_8x6mm_P1.27mm_EP3.4x4.3mm; Mfr.Part W25N04KVZEIR
Y1: 40 MHz; Crystal_SMD_3225-4Pin_3.2x2.5mm; Mfr.Part X322540MPB4SI
Y2: 32.768kHz; Oscillator_SMD_SeikoEpson_SG8002CE-4Pin_3.2x2.5mm; Mfr.Part OK2EL89CJI-111YLC-32.768K

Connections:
+3V8: C9.1, C17.1, D2.2 (A), J8.1, L2.1, R18.1, U2.9 (VIN)
+6V: C14.1, C26.1, C29.1, C30.1, C31.1, C32.1, J3.2, J4.2, J5.2, J6.2, R1.1, U2.14 (VOUT), U2.15 (VOUT), U2.16 (VOUT)
/Action: RN2.8 (R1.2), U4.44 (MTCK)
/BOOT: R16.2, SW3.2, U4.5 (GPIO0)
/BUZ: R14.2, U4.27 (GPIO21)
/CHIP_PU: C33.1, R15.2, SW2.2, U4.4 (CHIP_PU)
/DN: U3.6 (I/O1), U4.25 (GPIO19/USB_D-)
/DP: U3.4 (I/O2), U4.26 (GPIO20/USB_D+)
/FSPI_CLK: RN3.1 (R1.1), U4.17 (GPIO12)
/FSPI_CS0: RN3.3 (R3.1), U4.15 (GPIO10)
/FSPI_D: RN3.2 (R2.1), U4.16 (GPIO11)
/FSPI_HD: RN3.4 (R4.1), U4.14 (GPIO9)
/FSPI_Q: RN6.8 (R1.2), U4.18 (GPIO13)
/FSPI_WP: RN6.7 (R2.2), U4.19 (GPIO14)
/IMU_INT: U4.11 (GPIO6), U5.4 (INT1/INT)
/LD_CS: U4.45 (MTDO), U9.11 (SRCLK)
/LD_D: U4.28 (SPICS1), U9.14 (SER)
/LD_SCK: U4.13 (GPIO8), U9.12 (RCLK)
/OFF: R4.2, R6.1, U1.3 (EN), U4.43 (GPIO38)
/RXD0: J7.3, RN2.7 (R2.2), U4.50 (U0RXD)
/SCL: J2.2, R11.2, U4.24 (GPIO18), U6.3 (SCL), U7.2 (SCK/SCL)
/SDA: J2.1, R12.2, U4.23 (GPIO17), U6.4 (SDA), U7.4 (SDI/SDA)
/SERVOA: J3.1, U4.38 (GPIO33)
/SERVOB: J4.1, U4.39 (GPIO34)
/SERVOC: J5.1, U4.40 (GPIO35)
/SERVOD: J6.1, U4.41 (GPIO36)
/SERVOEN: JP1.1 (A), Q2.2 (G), R20.1, U4.42 (GPIO37)
/TX0_RAW: R13.2, RN2.6 (R3.2), U4.49 (U0TXD)
/TXD0: J7.4, R13.1
/VSPI_CLK: RN1.2 (R2.1), U4.9 (GPIO4)
/VSPI_CS: RN1.1 (R1.1), U4.10 (GPIO5)
/VSPI_D: RN1.3 (R3.1), U4.7 (GPIO2)
/VSPI_Q: RN1.4 (R4.1), U4.6 (GPIO1)
/V_ADC: R18.2, R19.1, U4.12 (GPIO7)
GND: AE1.2 (Shield), C2.2, C3.2, C4.2, C5.2, C6.2, C7.2, C8.2, C9.2, C10.1, C11.1, C12.2, C13.1, C14.2, C15.2, C16.2, C17.2, C18.1, C19.2, C20.1, C21.2, C22.2, C23.2, C24.2, C25.1, C27.2, C28.2, C32.2, C33.2, C34.2, C35.2, C36.2, C37.2, D5.1 (K), D6.1 (K), D7.1 (K), D8.1 (K), J1.A1 (GND), J1.A12 (GND), J1.B1 (GND), J1.B12 (GND), J2.3, J7.2, J8.2, Q1.2 (E), Q2.3 (S), R3.2, R6.2, R7.2, R8.2, R9.2, R19.2, R20.2, SW2.1, SW3.1, U1.2 (GND), U2.11 (NC), U2.12 (NC), U2.20 (AGND), U2.21 (PGND), U3.2 (GND), U4.51 (GPIO45), U4.52 (GPIO46), U4.57 (GND), U5.6 (GND), U5.7 (RESV), U5.11 (RESV), U6.1 (NC), U6.5 (GND), U6.6 (NC), U7.3 (VSS), U7.8 (VSS), U7.9 (VSS), U9.8 (GND), U9.13 (~OE), U10.4 (GND), Y1.2, Y1.4, Y2.2 (GND)
unnamed: AE1.1 (A), C36.1, L3.2
unnamed: BZ1.1 (+), C16.1, D1.1 (K), D2.1 (K), R21.2, SW1.1, U1.1 (VIN)
unnamed: BZ1.2 (-), Q1.3 (C), R21.1
unnamed: C1.2, L2.2, R2.1, U2.4 (SW), U2.5 (SW), U2.6 (SW), U2.7 (SW)
unnamed: C5.1, L1.2, U4.2 (VDD3P3), U4.3 (VDD3P3)
unnamed: C13.2, R5.2
unnamed: D1.2 (A), J1.A4 (VBUS), J1.A9 (VBUS), J1.B4 (VBUS), J1.B9 (VBUS)
unnamed: D5.2 (A), RN2.4 (R4.1)
unnamed: D6.2 (A), RN2.3 (R3.1)
unnamed: D7.2 (A), RN2.2 (R2.1)
unnamed: D8.2 (A), RN2.1 (R1.1)
unnamed: J1.A5 (CC1), R9.1
unnamed: J1.B5 (CC2), R8.1
unnamed: J1.A6 (D+), J1.B6 (D+), U3.3 (I/O2)
unnamed: J1.A7 (D-), J1.B7 (D-), U3.1 (I/O1)
unnamed: C26.2, C29.2, C30.2, C31.2, J3.3, J4.3, J5.3, J6.3, Q2.1 (D)
unnamed: JP1.2 (C), U2.2 (EN)
unnamed: Q1.1 (B), R14.1
unnamed: R4.1, SW1.2
unnamed: RN1.8 (R1.2), U5.12 (~CS/VDDIO)
unnamed: RN1.7 (R2.2), U5.13 (SCLK/SCL)
unnamed: RN1.6 (R3.2), U5.14 (SDIO/SDI/SDA)
unnamed: R10.2, RN1.5 (R4.2), U5.1 (SDO/ADO)
unnamed: RN3.8 (R1.2), U10.6 (CLK)
unnamed: RN3.7 (R2.2), U10.5 (DI)
unnamed: R17.1, RN3.6 (R3.2), U10.1 (~CS)
unnamed: RN3.5 (R4.2), U10.7 (~HOLD)
unnamed: RN4.1 (R1.1), U9.3 (QD)
unnamed: RN4.8 (R1.2), U8.2 (D)
unnamed: RN4.2 (R2.1), U9.2 (QC)
unnamed: RN4.7 (R2.2), U8.4 (C)
unnamed: RN4.3 (R3.1), U9.1 (QB)
unnamed: RN4.6 (R3.2), U8.6 (B)
unnamed: RN4.4 (R4.1), U9.15 (QA)
unnamed: RN4.5 (R4.2), U8.7 (A)
unnamed: RN5.1 (R1.1), U9.7 (QH)
unnamed: RN5.8 (R1.2), U8.5 (DP)
unnamed: RN5.2 (R2.1), U9.6 (QG)
unnamed: RN5.7 (R2.2), U8.10 (G)
unnamed: RN5.3 (R3.1), U9.5 (QF)
unnamed: RN5.6 (R3.2), U8.9 (F)
unnamed: RN5.4 (R4.1), U9.4 (QE)
unnamed: RN5.5 (R4.2), U8.1 (E)
unnamed: RN6.1 (R1.1), U10.2 (DO)
unnamed: RN6.2 (R2.1), U10.3 (~WP)
unnamed: C1.1, U2.8 (BOOT)
unnamed: C18.2, R5.1, U2.18 (COMP)
unnamed: R1.2, R3.1, U2.17 (FB)
unnamed: R2.2, U2.3 (FSW)
unnamed: R7.1, U2.19 (ILIM)
unnamed: C20.2, U2.10 (SS)
unnamed: C19.1, U2.1 (VCC)
unnamed: C35.1, L3.1, U4.1 (LNA_IN)
unnamed: C6.1, C7.1, U4.29 (VDD_SPI)
unnamed: C28.1, U4.53 (XTAL_N), Y1.1
unnamed: C27.1, U4.54 (XTAL_P), Y1.3
unnamed: C37.1, U5.9 (INT2/FSYNC/CLKIN), Y2.3 (OUT)
VDD: C2.1, C3.1, C4.1, C8.1, C10.2, C11.2, C12.1, C15.1, C21.1, C22.1, C23.1, C24.1, C25.2, C34.1, J2.4, J7.1, JP1.3 (B), L1.1, R10.1, R11.1, R12.1, R15.1, R16.1, R17.2, RN2.5 (R4.2), U1.5 (VOUT), U3.5 (VBUS), U4.20 (VDD3P3_RTC), U4.46 (VDD3P3_CPU), U4.55 (VDDA), U4.56 (VDDA), U5.5 (VDDIO), U5.8 (VDD), U6.2 (VDD), U7.1 (VDDIO), U7.5 (SDO), U7.6 (CSB), U7.10 (VDD), U8.3 (CA), U9.10 (~SRCLR), U9.16 (VCC), U10.8 (VCC), Y2.1 (OE), Y2.4 (Vcc)

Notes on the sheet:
These resistors near ESP

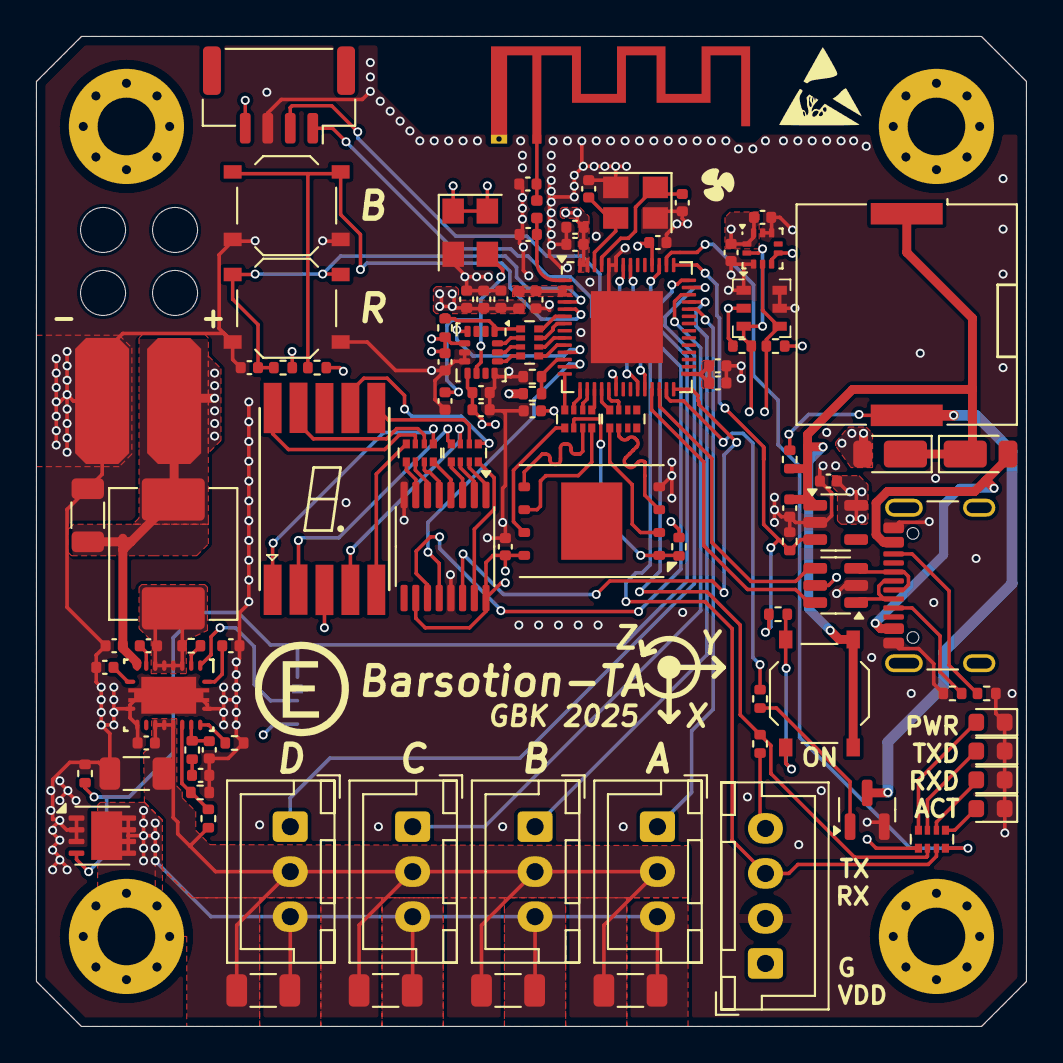
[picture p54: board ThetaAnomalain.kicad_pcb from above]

Board: 4 copper layers, 55.0 x 55.0 mm, 105 parts (1 on the bottom side), 93 nets.

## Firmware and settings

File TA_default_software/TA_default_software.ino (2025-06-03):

#include "Sevseg595_Barsotion.h"
//https://github.com/Barsy-Barsevich/Sevseg595_Barsotion
/**
 * A simple 7-segment via 74hc595 library
 * 
 * Available symbols:
 * Hex numbers:
 * 0 1 2 3 4 5 6 7 8 9 A b c d E F
 * Non-hex letters:
 * G H h I i J L n O o P q r S t U u Y
 * Special symbols:
 * _ - = [ ] " ' . ,
 * Space
 * 
 * 7-segment & 74hc595 wiring:
 * msb_first = true:
 * |Q0|Q1|Q2|Q3|Q4|Q5|Q6|Q7|
 * |A |B |C |D |E |F |G |DP|
 * msb_first = false:
 * |Q0|Q1|Q2|Q3|Q4|Q5|Q6|Q7|
 * |DP|G |F |E |D |C |B |A |
 * 
 * Common cathode - invert = false
 * Common anode - invert = true
 */


const int cs = 8;  //RCLK - 12 pin
const int sck = 40;  //SRCLK - 11 pin
const int d = 26;   //SER - 14 pin

void cs_set(uint8_t val) {digitalWrite(cs, val);}
void sck_set(uint8_t val) {digitalWrite(sck, val);}
void data_set(uint8_t val) {digitalWrite(d, val);}

sevseg_t sevseg;


void setup()
{
    pinMode(38, OUTPUT);
    digitalWrite(38, HIGH);
    Serial.begin(115200);
    pinMode(39, OUTPUT);
    pinMode(cs, OUTPUT);
    pinMode(sck, OUTPUT);
    pinMode(d, OUTPUT);
    sevseg.msb_first = true;
    sevseg.invert = true; //common cathode
    sevseg.cs_pin_set = cs_set;
    sevseg.sck_pin_set = sck_set;
    sevseg.data_pin_set = data_set;
}

void loop()
{
    Serial.println("Goida!");
    digitalWrite(39, LOW);
    sevseg_print(&sevseg, 'G');
    delay(500);
    sevseg_print(&sevseg, 'o');
    delay(500);
    sevseg_print(&sevseg, 'i');
    delay(500);
    sevseg_print(&sevseg, 'd');
    delay(500);
    sevseg_sh(&sevseg, ~0b00101010);
    delay(500);
    sevseg_print(&sevseg, ' '); //printing a space
    digitalWrite(39, HIGH);
    delay(2000);
}
